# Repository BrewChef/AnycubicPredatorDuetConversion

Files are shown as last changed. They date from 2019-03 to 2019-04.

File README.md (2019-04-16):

This is a repository for different Duet conversion and the Anycubic Predator.

The work is still in progress and no warranty are given.

Duet Generic configs
=============
This are generic Duet configs.  In the config you can choose to use "stock"  or 12V Fans / Bondtech extruder

Duet Smarteffector Ethernet configs
=============
This are the folder high customized Duet configs.   
Parts in use:  
* Duet Smarteffector
* Duet 2 Ethernet
* E3D V6 hotend with microswiss nozzles
* Hayden’s Magball-Carbon Rods.
* 25mm silika wool to isolate the heatbed  
* complete new wiring (except the heatbed)
* all Fans noctua (except the 2 radial printcooler)
* flexed PSU housing open, to get better airflow and lower noise
* Silikon damper on stepper

instructions
===============================
space to upload wirings or other instructions

printables
===============================
space to upload printobjects

instructions
===============================
space to upload profiles

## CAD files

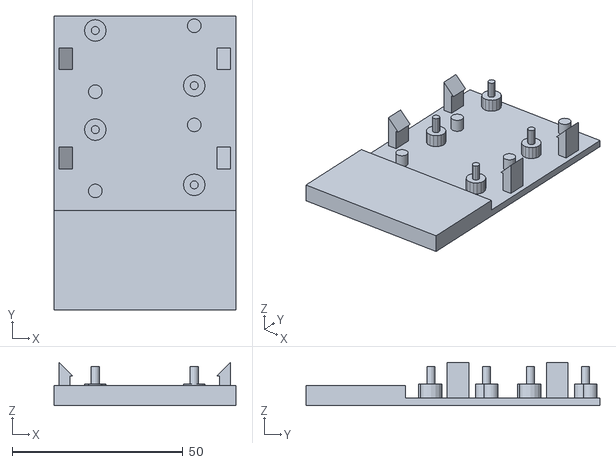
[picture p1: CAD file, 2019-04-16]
printables/buck_converter_mount.stl
53.3 x 85.9 x 12.7

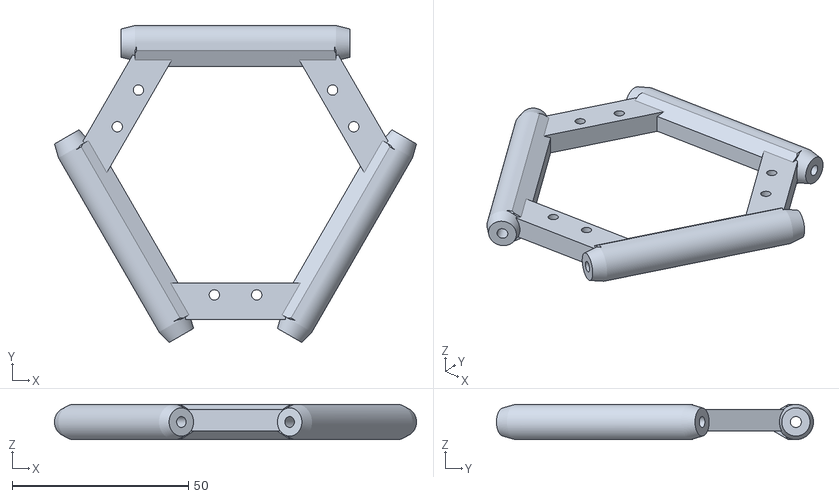
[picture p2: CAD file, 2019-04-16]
printables/ConversionDuetSmarteffectorPredator.stl
102.6 x 89.9 x 10.0

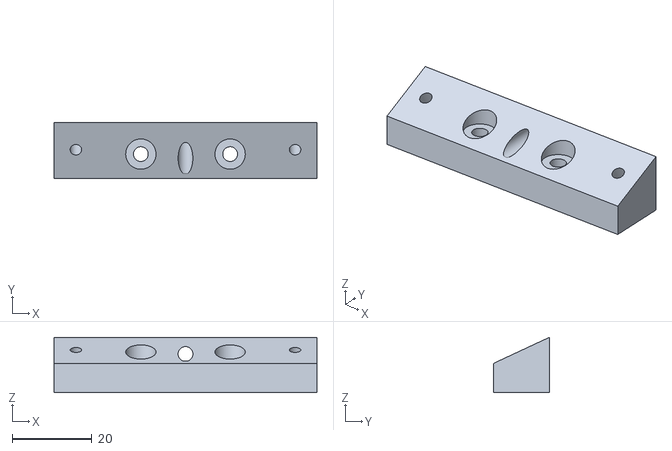
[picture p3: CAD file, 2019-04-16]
printables/CarriageAdapterforHaydenRodsV2.stl
66.0 x 14.0 x 13.9

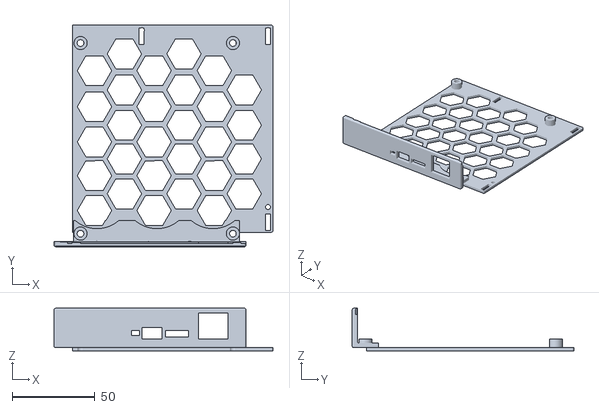
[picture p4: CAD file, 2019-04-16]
printables/DuetPredatorholder_MAESTRO.stl
132.2 x 133.8 x 25.7

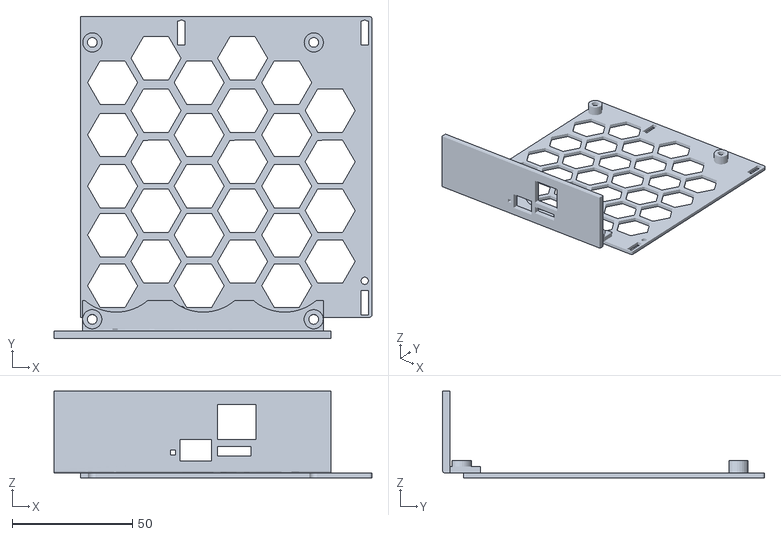
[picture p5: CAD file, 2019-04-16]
printables/DuetPredatorholder_ETHERNET.stl
132.1 x 133.8 x 36.0

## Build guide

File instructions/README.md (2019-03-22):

watch https://www.youtube.com/watch?v=BgkJVgFnPaE for first idea and have this opened or printed for reference https://duet3d.dozuki.com/Wiki/Duet_2_Maestro_Wiring_Diagram

- connect hotend, bed and their thermistors to the respective ports at the Duet (Bed and E0)
- maybe you've got to extend the hotend cable (I had)
- connect motors  X, Y, Z and E to the new board as usual, you can recrimp new connectors, but you don't have to (see video)
- connect the endstops of X, Y and Z to the respective ports on the Duet. 
  Use the pinlayout from the board and dont look at the wirecolours.
  Take care of the different pins by recrimping or using jumper cables 
- connect the filament runout sensor to the E0 endstop and the Level sensor to E1 endstop, same as above
- if you want to replace the hotend cooling fan by e.g. a noctua with 12V, than you have to add an extra wire to the cabling down to the effector
- maybe also one or more additional wires for a different level sensor?

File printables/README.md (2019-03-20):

This is the folder for the 3D printables.
i.E. boardholder, etc.

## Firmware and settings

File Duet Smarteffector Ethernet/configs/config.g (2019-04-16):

; Configuration file for Duet Ethernet
; executed by the firmware on start-up
;
; generated by RepRapFirmware Configuration Tool v2 on Sat Mar 16 2019 23:24:37 GMT+0100 (Mitteleuropäische Normalzeit)
; edited by nealz

;### General preferences ###
M111 S0						; Debug off
G90							  ; Send absolute coordinates...
M83							  ; ...but relative extruder moves
M555 P2						; Set output to look like Marlin

;### Network ###
M550 P"Anycubic Predator"			; Set machine name
M551 Preprap						; Machine password (used when you connect Duet Web Control or via FTP)
M552 P192.168.0.180 S1				; Enable network and acquire dynamic address via DHCP
M586 P0 S1							; Enable HTTP
M586 P1 S1							; Enable FTP (enable or disable for your needs)
M586 P2 S1							; Enable Telnet (enable or disable for your needs)

;### Drives ###
M569 P0 S0  						; Drive 0 (X) goes forwards, stealthChop mode, switch from stealthChop to to spreadCycle mode only at high speeds
M569 P1 S0 							; Drive 1 (Y) same as Drive 0 
M569 P2 S0 							; Drive 2 (Z) same as Drive 0 
M569 P3 S0 							; Drive 3 (Extruder) goes backwards, spreadCycle mode
M350 X16 Y16 Z16 E16 I1				; Configure microstepping with interpolation
M92 X80.00 Y80.00 Z80.00 E415.00	; Set steps per mm  (Extruder Bondtech clone!)

;### Speed, Jerks ###
M201 X1100.00 Y1100.00 Z1100.00 E1100.00	; Set accelerations (mm/s^2)
M203 X9000.00 Y9000.00 Z9000.00 E4800.00	; Set maximum speeds (mm/min)
;M566 X900.00 Y900.00 Z900.00 E1500.00		; Set maximum instantaneous speed changes (mm/min)
M566 X600.00 Y600.00 Z600.00 E1200.00		; Set maximum instantaneous speed changes (mm/min) changed 20180411 1330

M906 X1000.00 Y1000.00 Z1000.00 E800.00 I30 	; Set motor currents (mA) and motor idle factor in per cent
M84 S30                                     	; Set idle timeout

;### Delta configuration ###
M665 R227 L440 B185 H425		; Set delta radius, diagonal rod length, printable radius and homed height 
M666 X0 Y0 Z0					; Put your endstop adjustments here, or let auto calibration find them

;### Axis Limits ###
M208 Z0 S1						; Set minimum Z

;### Endstops ###
M574 X2 Y2 Z2 S1				; all endstops at high end, active high

;### Z-Probe ###
M558 P8 R0.4 F1200 				; Set Z probe type to switch and the dive height + speeds
G31 P100 X0 Y0 Z-0.1			; Set Z probe trigger value, offset and trigger height - must be adjusted for your machine
M557 R185 S20 					; Define mesh grid

;### Heaters ###
; H0 = BED
; H1 = Hotend
M305 P0 T100000 B3950 R2200					; Set thermistor + ADC parameters for heater 0 (thermistor type guessed)
M305 P0 T100000 B4725 C7.060000e-8 R4700	; TESTNIELS
M305 P1 B4725 C7.060000e-8					; Set thermistor + ADC parameters for heater 1 
M307 H0 A137.8 C533.3 D1.5 V24.3 B0			; PID parameters for heatbed - must be adjusted for your machine                   
M307 H1 A503.5 C107.0 D9.3 V24.3 B0 		; PID parameters for hotend - must be adjusted for your machine                   
M143 H0 S130								; Set temperature limit for heater 0 to 120C
M143 H1 S280								; Set temperature limit for heater 1 to 280C

;### Fans ###
M106 P0 S0 I0 F100 H-1 C"Print Cooling"		; Set fan 0 value, PWM signal inversion and frequency. Thermostatic control is turned off
M106 P1 S1 I0 F100 H1 T45 C"Heatsink"		; Set fan 1 value, PWM signal inversion and frequency. Thermostatic control is turned on

;### Tools ###
M200 D1.75						; turn volumetric control off
M563 P0 D0 H1 F0				; Define tool 0, extruder 0, Heater 1, Fan 0
G10 P0 X0 Y0 Z0					; Set tool 0 axis offsets
G10 P0 R0 S0					; Set initial tool 0 active and standby temperatures to 0C
T0								; select tool 0
;M572 D0 S0.1					; Pressure Advance

;### Filament Sensor ###
M591 D0 P0 C3 S1

; Automatic saving after power loss is not enabled

;### enable use of sys/config-override.g###
M501						; Load saved parameters from non-volatile memory
 

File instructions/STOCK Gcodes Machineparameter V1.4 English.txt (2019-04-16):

;[[After the semicolon is a comment, please modify the corresponding parameters according to the comment, the command after the semicolon will be ignored]]
The basic format is Mxxx Ixxx, Mxxx Txxx or Mxxx Sxxx, where Ixx (which is the letter I, the first letter of the integer, not the number 1) followed by an integer, which can be either decimal or hexadecimal (starting with 0x) ), followed by Sxx is a floating point number
;
[Print off and power off save] need to use the module together, if there is no related module, please set it to 0;
M8000 I1 ; Power-off save support or not, I1 means support, I0 means no support, restart will take effect after setting
M8001 I0; print shutdown support or not, I1 means support, I0 means no support, restart will take effect after setting
;
[Stepper motor direction control] The direction of I1 and I-1 is just opposite, so if the motor direction is wrong, either change the wiring or change the direction parameter.
M8002 I1; ;X stepper motor direction, I1 or I-1
M8003 I1 ; Y stepper motor direction
M8004 I1 ; Z stepper motor direction
M8005 I-1 ; E stepper motor direction
M8005 I1 E2 ; Set the second E stepper motor direction, I1 or I-1. If there are no multiple nozzles, please ignore this configuration.
M8005 I1 E3 ; Set the third E stepping motor direction, I1 or I-1. If there is no multi-nozzle, please ignore this configuration. The three nozzles only support three in and one out.

;[XYZ axis extrusion head/platform movement configuration] only affects the actual movement direction of the manual interface button;;;;;;;;;;;;;;;;;;;;;;;;;;
M8005 X0 ; 0: X-axis direction Extrusion head movement
; 1: X-axis direction Platform movement Currently, most of the machines on the market are X-axis extrusion head movements.
M8005 Y0 ; 0: Y-axis direction Extrusion head movement
; 1: Y-axis direction Platform motion Currently, the Y-axis of the structure of I3 is platform motion.
The delta, ultimaker and makerbot's Y-axis is the extrusion head movement
M8005 Z0 ; 0: Z-axis direction Extrusion head movement, current I3 structure and delta structure Z-axis is the extrusion head movement,
; 1: Z-axis direction platform motion, ultimaker and makerbot structure Z-axis is platform movement
;



;[XYZE default speed/acceleration setting] speed in mm/s, acceleration in mm/s^2
M8006 I50; the maximum starting speed, when the speed of movement has passed this speed, it will start at this speed.
This speed is mainly to prevent out of step, this value is too small, will cause the rail angle bulge when rounding
M8007 I25; the maximum rail bending speed value (corresponding to the jerk speed in the open source firmware), if the actual rail bending speed of the motion is greater than this value,
; will force the movement to slow down. When filling, there will be a lot of reciprocating motions, this value is large, the noise is large, and it is easy to lose steps.
; This value is small, slow, and print quality is relatively poor when printing speed is high
M8008 I1100 ; Acceleration, the larger the value, the larger the average speed of actual operation, but the noise is also large, the value is small, and the actual speed will be smaller.
;

; [E-axis independent speed / acceleration setting] speed in mm / s, acceleration in mm / s ^ 2
Note: If the E-axis is a step-down motor, the speed and acceleration of E should be reduced because of the deceleration, otherwise the E-axis will be out of step.
M8007 E25; maximum rail bending speed value (corresponding to jerk speed in open source firmware), if the actual rail bending speed of the motion is greater than this value
M8008 E1100 ; acceleration, the larger the value, the greater the average speed of actual operation, the bending speed and acceleration of the E-axis will affect the brushed bridge
;


;[[[step related parameters]]] After the parameters are set, please print a cube, then measure the size with a ruler to confirm that there is no problem with the parameters.
If the machine is a delta structure, set the motor parameters of XYZ to be the same, and the Z parameters are the same as the XY calculation method.
M8009 S0.0125; [XY value of each step of XY] is 20 teeth, the pitch is 2mm (mxl specification, 2gt is 2mm), 1.8 degree stepper motor,
; 16 subdivision, then (20 * 2) / ((360 / 1.8) * 16)
;M8009 X0.0125 Y0.0125 ; If you need to set the X, Y stepper motor parameters independently, you can use this command
;
M8010 S0.0125 ; [Z value of each step of Z] On a non-delta machine, calculate the formula: lead / ((360 / 1.8) * 16).
If it is on a delta machine, set it to the same as the XY parameter.
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

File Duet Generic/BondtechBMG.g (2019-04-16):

; additional lines for a Bondtech BMG (Clone) extruder

; Drive
M569 P3 S0 D2           ; Drive 3 (Extruder) goes forwards, spreadCycle mode
M92  E415.00            ; Set steps per mm

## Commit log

2019-03-21 reduce extrusion multiplier to 1,08
2019-03-21 Add files via upload
    Gcode from the original firmware as a source of information - not needed for Duet
    [Gcodes Machineparameter V1.4 English.txt]
2019-03-21 revision of config files
    [12V.g, BondtechBMG.g, bed.g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]
2019-03-23 turn volumetric control off
    [config.g]
2019-04-16 Updated struc
    [12V.g, BondtechBMG.g, Gcodes Machineparameter V1.4 English.txt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]
2019-04-16 Update @ structs
    [12V.g, BondtechBMG.g, bed.g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]
2019-04-16 Update configs
    [bed.g, cancel.g, config.g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]
